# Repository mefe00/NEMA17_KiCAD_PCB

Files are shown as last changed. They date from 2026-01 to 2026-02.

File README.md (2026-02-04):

# NEMA17_KiCAD_PCB

step_motor
step

Kartın üzerinde kullanılan bazı komponentlerin yanlış seçilmesinden dolayı kartın montajı gerçekleştirilemiyor. Aslında sadece TMC2208'in shild olarak seçilmesinden kaynaklı pin delikleri yanlış seçilmiştir. Kartın ikinci versiyonunda shild ve direkt TMC2208 çipi kullanılarak kart yenilenecektir.

V2 buradan paylaşılacaktır.

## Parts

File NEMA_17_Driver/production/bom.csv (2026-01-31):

Designator | Footprint | Quantity | Value | LCSC Part #
C10, C13, C14, C15, C16, C20, C21 | 0402 | 7 | 100nF
C11, C18 | 0402 | 2 | 10uF
C17, C6, C7 | 0402 | 3 | 1uF
C19 | 0402 | 1 | 10nF
C2 | C_Elec_8x10.2 | 1 | 4,7uF
C22, C24 | 0603 | 2 | 20pF
C3, C4 | 0402 | 2 | 0.1uF
C5 | 0402 | 1 | 4.7nF
C8 | 0603 | 1 | 0.01uF
C9 | 0805 | 1 | 100uF
D3 | D_SMA | 1 | SS34
D4 | 0402 | 1 | GREEN
D5 | 0402 | 1 | RED
D6 | 0402 | 1 | BLUE
D7 | D_MiniMELF | 1 | LL4148
D8 | D_SMA | 1 | SMAJ40A
FB1 | 0402 | 1 | FerriteBead
J1 | SolderWire-0.75sqmm_1x02_P7mm_D1.25mm_OD3.5mm | 1 | Conn_01x02_Socket
J10, J11 | PinSocket_1x08_P2.00mm_Vertical | 2 | Conn_01x08_Socket
J12 | Molex_KK-254_AE-6410-04A_1x04_P2.54mm_Vertical | 1 | Conn_01x04_Socket
J2, J4 | Hirose_DF13-04P-1.25DSA_1x04_P1.25mm_Vertical | 2 | Conn_01x04_Socket
J6, J8 | Hirose_DF13-02P-1.25DSA_1x02_P1.25mm_Vertical | 2 | Conn_01x02_Socket
J7 | Hirose_DF13-04P-1.25DS_1x04_P1.25mm_Horizontal | 1 | Conn_01x04_Socket
L2 | L_Murata_DEM3512C | 1 | 33uH
Q1 | SOT-23 | 1 | AO3400A
R1, R2 | 0402 | 2 | 22R
R10, R18 | 0402 | 2 | 4.7k
R11 | 0603 | 1 | 4.7k
R12, R15, R4, R7, R8 | 0402 | 5 | 10k
R13, R14 | 0402 | 2 | 330R
R16, R3 | 0402 | 2 | 60R
R17, R19 | 0402 | 2 | 1k
R20, R6 | 0201 | 2 | 0
R5 | 0402 | 1 | 3.24k
R9 | 0402 | 1 | 100R
SW1 | SW_Push_1P1T_NO_CK_KMR2 | 1 | SW_Push
U1 | DFN-8-1EP_3x3mm_P0.65mm_EP1.55x2.4mm | 1 | MCP2542FDxMF
U2 | SOT-23-5 | 1 | AP2112K-3.3
U3 | SOIC-8_3.9x4.9mm_P1.27mm | 1 | TPS5420D
U4 | LQFP-48_7x7mm_P0.5mm | 1 | STM32F103C8Tx
U5 | SOIC8 | 1 | AS5600
Y1 | Crystal_SMD_5032-2Pin_5.0x3.2mm | 1 | Crystal

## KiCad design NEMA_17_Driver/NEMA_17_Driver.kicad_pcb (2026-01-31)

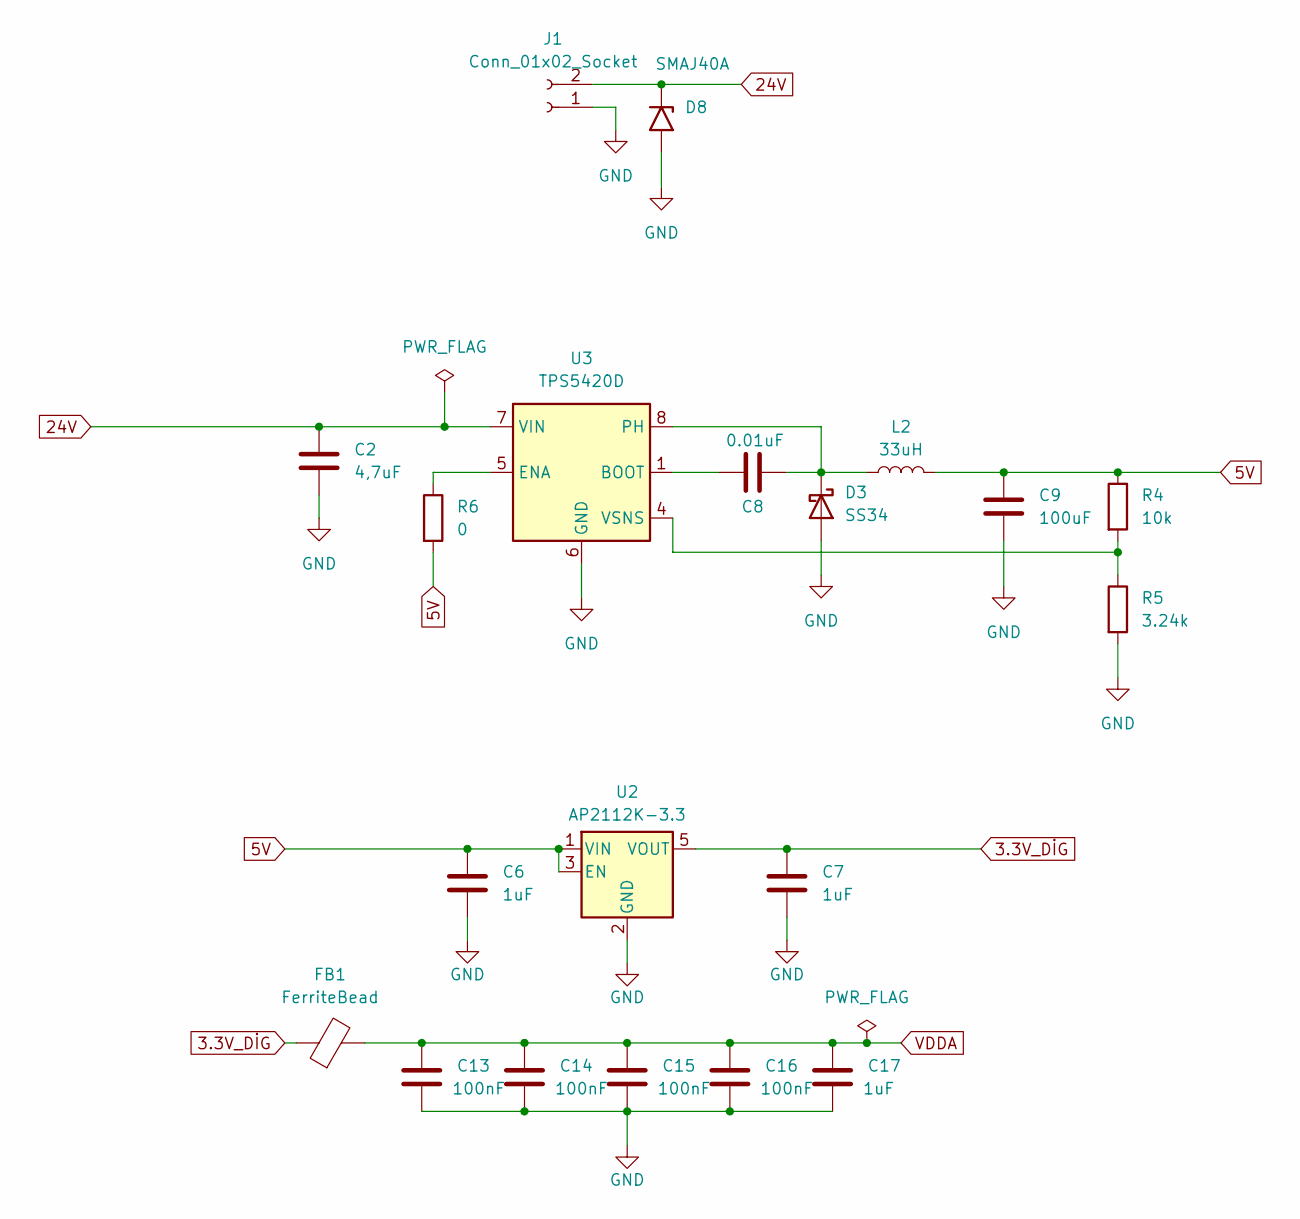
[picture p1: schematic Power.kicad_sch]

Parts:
C2: 4,7uF; C_Elec_8x10.2
C6, C7, C17: 1uF; C_0402_1005Metric
C8: 0.01uF; C_0603_1608Metric
C9: 100uF; C_0805_2012Metric
C13, C14, C15, C16: 100nF; C_0402_1005Metric
D3: SS34; D_SMA
D8: SMAJ40A; D_SMA
FB1: FerriteBead; L_0402_1005Metric
J1: Conn_01x02_Socket; SolderWire-0.75sqmm_1x02_P7mm_D1.25mm_OD3.5mm
L2: 33uH; L_Murata_DEM3512C
R4: 10k; R_0402_1005Metric
R5: 3.24k; R_0402_1005Metric
R6: 0; D_0201_0603Metric
U2: AP2112K-3.3; SOT-23-5
U3: TPS5420D; SOIC-8_3.9x4.9mm_P1.27mm

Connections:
3.3V_DİG: C7.1, FB1.1, U2.5 (VOUT); also elsewhere on the board
5V: C6.1, C9.1, L2.2, R4.1, R6.2, U2.1 (VIN), U2.3 (EN); also elsewhere on the board
24V: C2.1, D8.1 (A1), J1.2, U3.7 (VIN); also elsewhere on the board
GND: C2.2, C6.2, C7.2, C9.2, C13.2, C14.2, C15.2, C16.2, C17.2, D3.2 (A), D8.2 (A2), J1.1, R5.2, U2.2 (GND), U3.6 (GND); also elsewhere on the board
unnamed: C8.2, D3.1 (K), L2.1, U3.8 (PH)
unnamed: C8.1, U3.1 (BOOT)
unnamed: R6.1, U3.5 (ENA)
unnamed: R4.2, R5.1, U3.4 (VSNS)
VDDA: C13.1, C14.1, C15.1, C16.1, C17.1, FB1.2; also elsewhere on the board

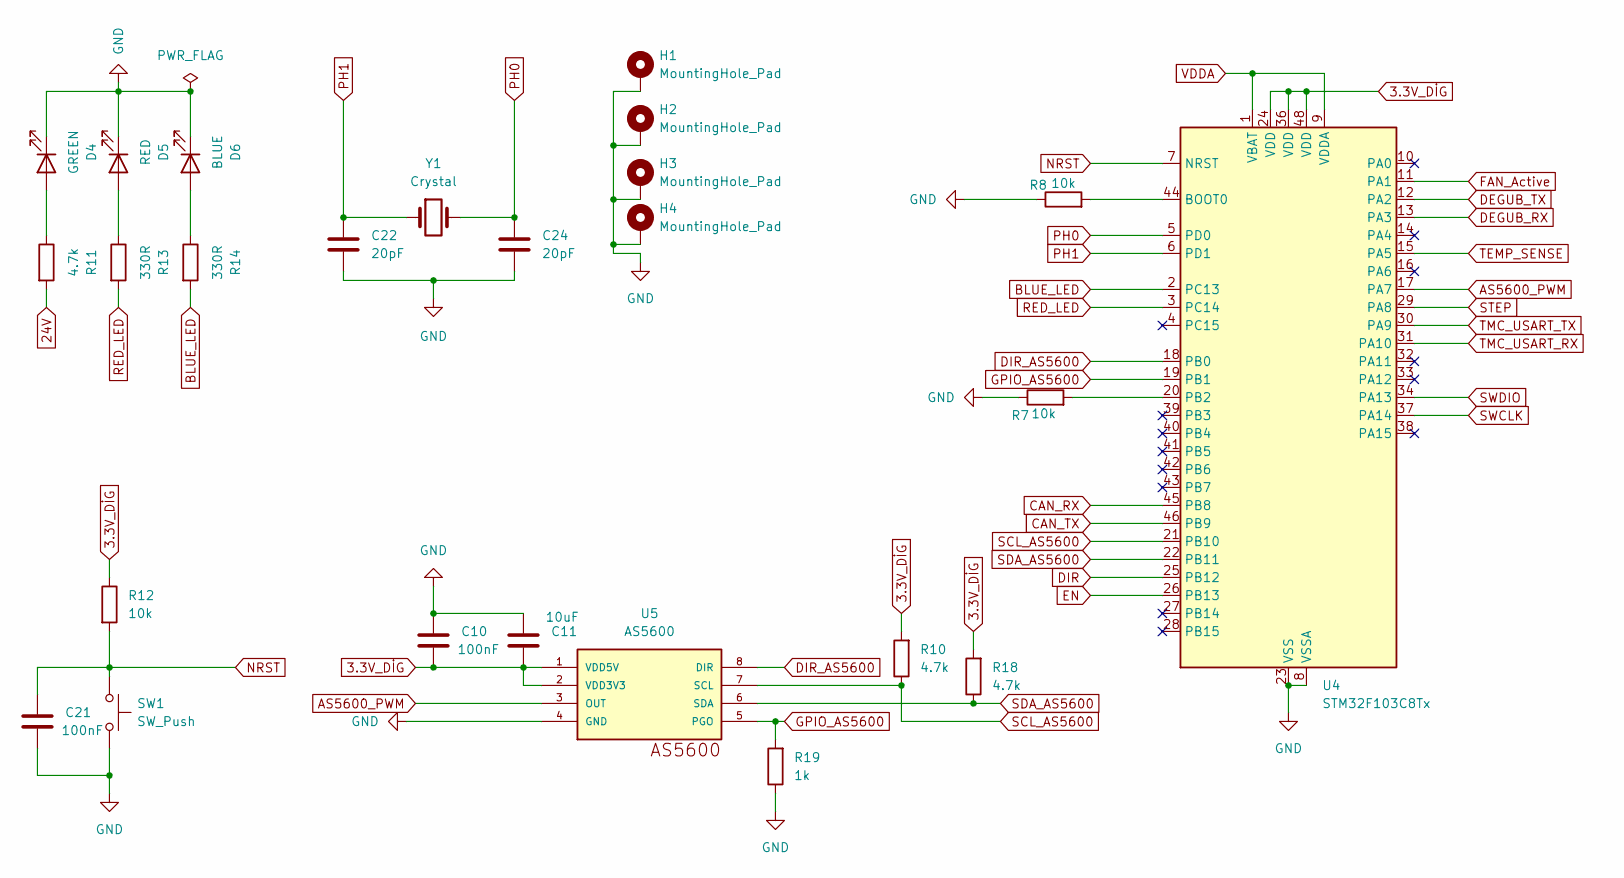
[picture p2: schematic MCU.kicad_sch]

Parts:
C10, C21: 100nF; C_0402_1005Metric
C11: 10uF; C_0402_1005Metric
C22, C24: 20pF; C_0603_1608Metric
D4: GREEN; LED_0402_1005Metric
D5: RED; LED_0402_1005Metric
D6: BLUE; LED_0402_1005Metric
H1, H2, H3, H4: MountingHole_Pad; MountingHole_3.5mm_Pad_Via
R7, R8, R12: 10k; R_0402_1005Metric
R10, R18: 4.7k; R_0402_1005Metric
R11: 4.7k; R_0603_1608Metric
R13, R14: 330R; R_0402_1005Metric
R19: 1k; R_0402_1005Metric
SW1: SW_Push; SW_Push_1P1T_NO_CK_KMR2
U4: STM32F103C8Tx; LQFP-48_7x7mm_P0.5mm
U5: AS5600; SOIC8
Y1: Crystal; Crystal_SMD_5032-2Pin_5.0x3.2mm

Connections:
3.3V_DİG: C10.2, C11.2, R10.2, R12.1, R18.2, U4.24 (VDD), U4.36 (VDD), U4.48 (VDD), U5.1 (VDD5V), U5.2 (VDD3V3); also elsewhere on the board
24V: R11.2; also elsewhere on the board
AS5600_PWM: U4.17 (PA7), U5.3 (OUT)
BLUE_LED: R14.2, U4.2 (PC13)
CAN_RX: U4.45 (PB8); also elsewhere on the board
CAN_TX: U4.46 (PB9); also elsewhere on the board
DEGUB_RX: U4.13 (PA3); also elsewhere on the board
DEGUB_TX: U4.12 (PA2); also elsewhere on the board
DIR: U4.25 (PB12); also elsewhere on the board
DIR_AS5600: U4.18 (PB0), U5.8 (DIR)
EN: U4.26 (PB13); also elsewhere on the board
FAN_Active: U4.11 (PA1); also elsewhere on the board
GND: C10.1, C11.1, C21.2, C22.2, C24.2, D4.1 (K), D5.1 (K), D6.1 (K), H1.1, H2.1, H3.1, H4.1, R7.1, R8.1, R19.1, SW1.2, U4.8 (VSSA), U4.23 (VSS), U4.35 (VSS), U4.47 (VSS), U5.4 (GND); also elsewhere on the board
GPIO_AS5600: R19.2, U4.19 (PB1), U5.5 (PGO)
NRST: C21.1, R12.2, SW1.1, U4.7 (NRST)
unnamed: D4.2 (A), R11.1
unnamed: D5.2 (A), R13.1
unnamed: D6.2 (A), R14.1
unnamed: R8.2, U4.44 (BOOT0)
unnamed: R7.2, U4.20 (PB2)
PH0: C24.1, U4.5 (PD0), Y1.2
PH1: C22.1, U4.6 (PD1), Y1.1
RED_LED: R13.2, U4.3 (PC14)
SCL_AS5600: R10.1, U4.21 (PB10), U5.7 (SCL)
SDA_AS5600: R18.1, U4.22 (PB11), U5.6 (SDA)
STEP: U4.29 (PA8); also elsewhere on the board
SWCLK: U4.37 (PA14); also elsewhere on the board
SWDIO: U4.34 (PA13); also elsewhere on the board
TEMP_SENSE: U4.15 (PA5); also elsewhere on the board
TMC_USART_RX: U4.31 (PA10); also elsewhere on the board
TMC_USART_TX: U4.30 (PA9); also elsewhere on the board
VDDA: U4.1 (VBAT), U4.9 (VDDA); also elsewhere on the board

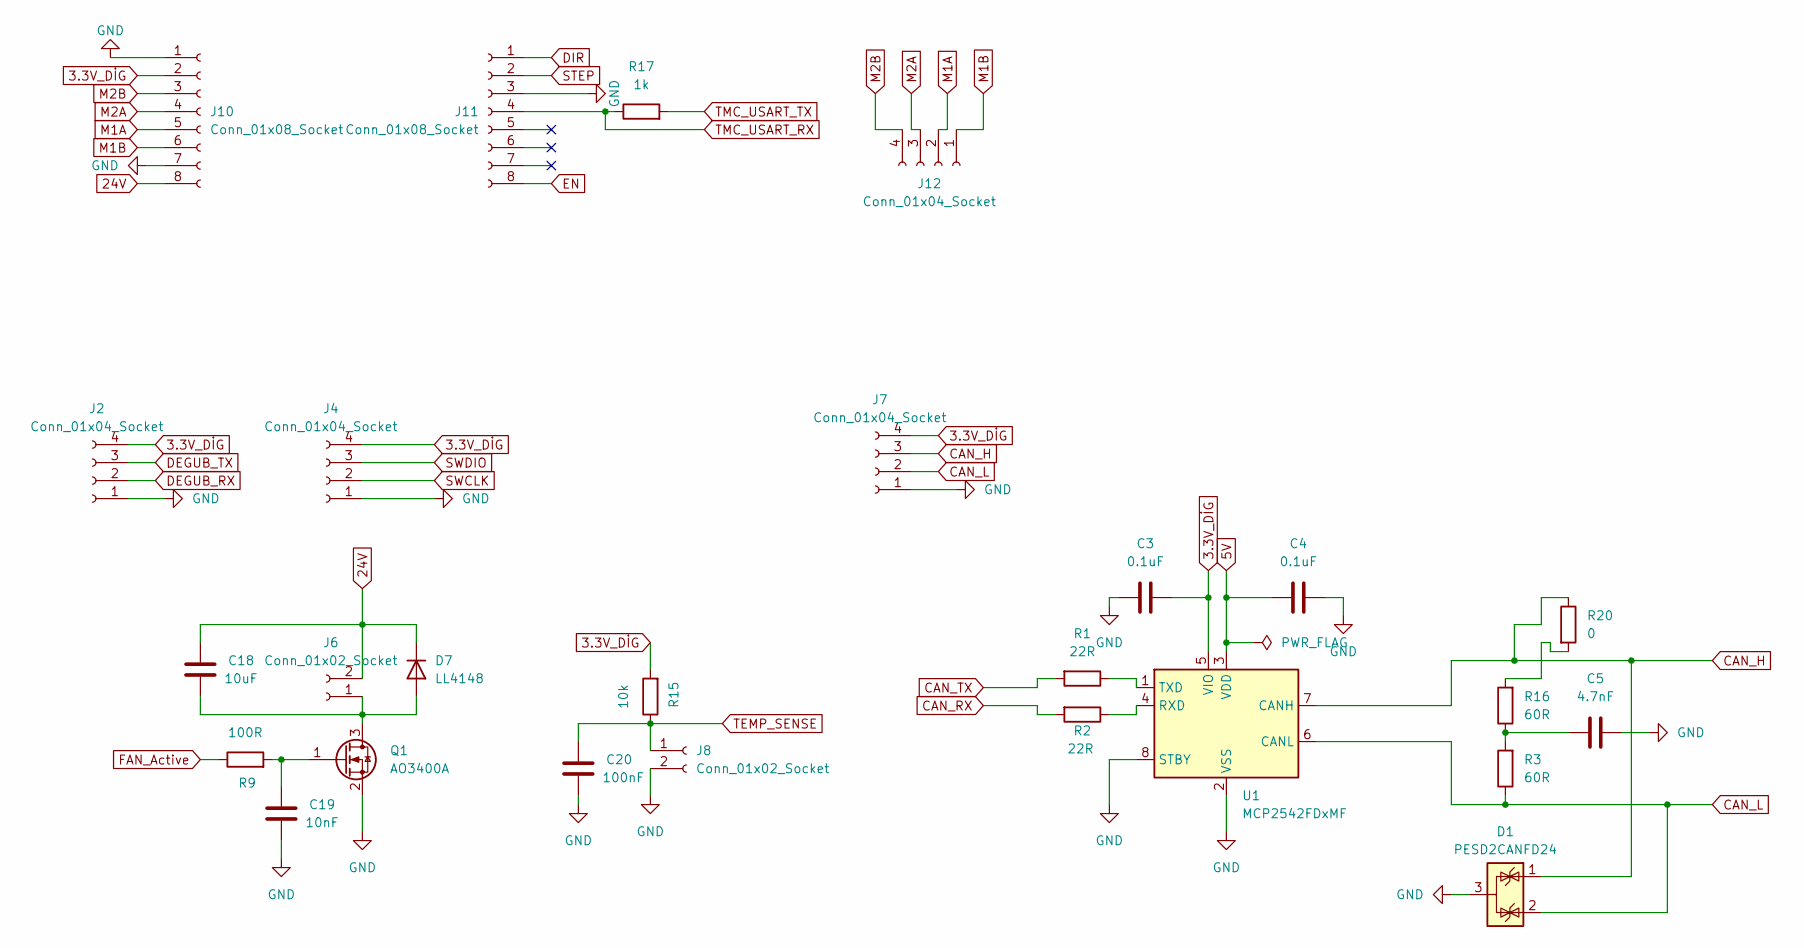
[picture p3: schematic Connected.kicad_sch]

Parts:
C3, C4: 0.1uF; C_0402_1005Metric
C5: 4.7nF; C_0402_1005Metric
C18: 10uF; C_0402_1005Metric
C19: 10nF; C_0402_1005Metric
C20: 100nF; C_0402_1005Metric
D1: PESD2CANFD24
D7: LL4148; D_MiniMELF
J2, J4: Conn_01x04_Socket; Hirose_DF13-04P-1.25DSA_1x04_P1.25mm_Vertical
J6, J8: Conn_01x02_Socket; Hirose_DF13-02P-1.25DSA_1x02_P1.25mm_Vertical
J7: Conn_01x04_Socket; Hirose_DF13-04P-1.25DS_1x04_P1.25mm_Horizontal
J10, J11: Conn_01x08_Socket; PinSocket_1x08_P2.00mm_Vertical
J12: Conn_01x04_Socket; Molex_KK-254_AE-6410-04A_1x04_P2.54mm_Vertical
Q1: AO3400A; SOT-23
R1, R2: 22R; R_0402_1005Metric
R3, R16: 60R; R_0402_1005Metric
R9: 100R; R_0402_1005Metric
R15: 10k; R_0402_1005Metric
R17: 1k; R_0402_1005Metric
R20: 0; R_0201_0603Metric
U1: MCP2542FDxMF; DFN-8-1EP_3x3mm_P0.65mm_EP1.55x2.4mm

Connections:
3.3V_DİG: C3.2, J2.4, J4.4, J7.4, J10.2, R15.2, U1.5 (VIO); also elsewhere on the board
5V: C4.1, U1.3 (VDD); also elsewhere on the board
24V: C18.1, D7.1 (K), J6.2, J10.8; also elsewhere on the board
CAN_H: D1.1 (K), J7.3, R20.1, U1.7 (CANH)
CAN_L: D1.2 (K), J7.2, R3.1, U1.6 (CANL)
CAN_RX: R2.2; also elsewhere on the board
CAN_TX: R1.2; also elsewhere on the board
DEGUB_RX: J2.2; also elsewhere on the board
DEGUB_TX: J2.3; also elsewhere on the board
DIR: J11.1; also elsewhere on the board
EN: J11.8; also elsewhere on the board
FAN_Active: R9.1; also elsewhere on the board
GND: C3.1, C4.2, C5.2, C19.2, C20.2, D1.3 (A), J2.1, J4.1, J7.1, J8.2, J10.1, J10.7, J11.3, Q1.2 (S), U1.2 (VSS), U1.8 (STBY), U1.9 (VSS); also elsewhere on the board
M1A: J10.5, J12.2
M1B: J10.6, J12.1
M2A: J10.4, J12.3
M2B: J10.3, J12.4
unnamed: C5.1, R3.2, R16.1
unnamed: C18.2, D7.2 (A), J6.1, Q1.3 (D)
unnamed: C19.1, Q1.1 (G), R9.2
unnamed: R16.2, R20.2
unnamed: R2.1, U1.4 (RXD)
unnamed: R1.1, U1.1 (TXD)
STEP: J11.2; also elsewhere on the board
SWCLK: J4.2; also elsewhere on the board
SWDIO: J4.3; also elsewhere on the board
TEMP_SENSE: C20.1, J8.1, R15.1; also elsewhere on the board
TMC_USART_RX: J11.4, R17.1; also elsewhere on the board
TMC_USART_TX: R17.2; also elsewhere on the board

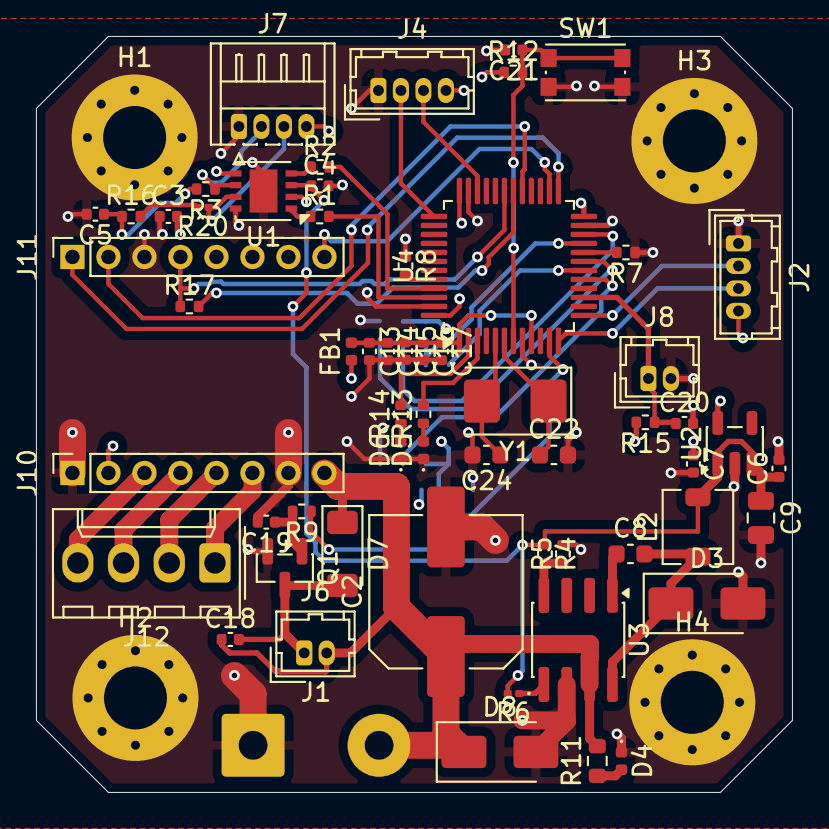
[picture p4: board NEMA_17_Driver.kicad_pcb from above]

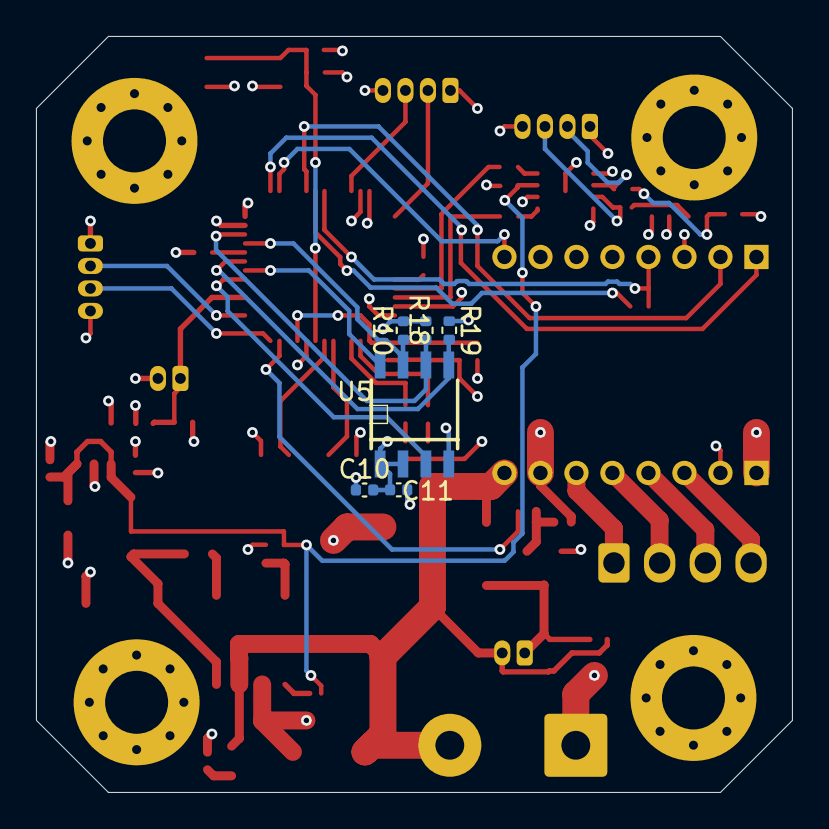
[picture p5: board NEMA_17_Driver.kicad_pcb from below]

Board: 4 copper layers, 42.0 x 42.0 mm, 70 parts (6 on the bottom side), 49 nets.
